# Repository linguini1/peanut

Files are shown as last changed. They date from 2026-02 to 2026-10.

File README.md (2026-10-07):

# Peanut 

A modern, tiny, and hackable altimeter for hobby rocketry.

[Peanut is certified as open-source hardware by the Open Source Hardware
Association (CA000081).][oshw-cert]

<p align="center">
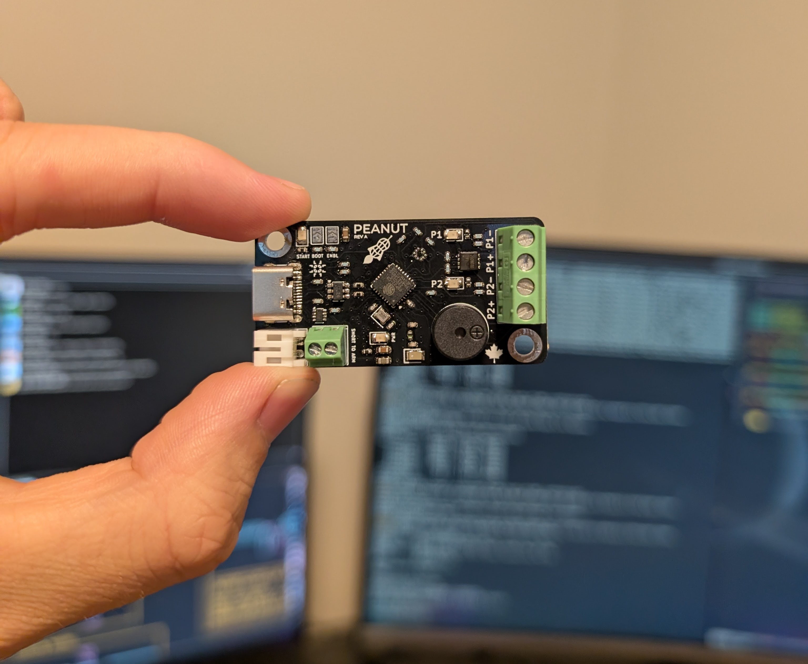
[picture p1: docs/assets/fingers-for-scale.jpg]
    
    <br/>
    Peanut Altimeter with my fingers for scale
</p>

<p align="center">
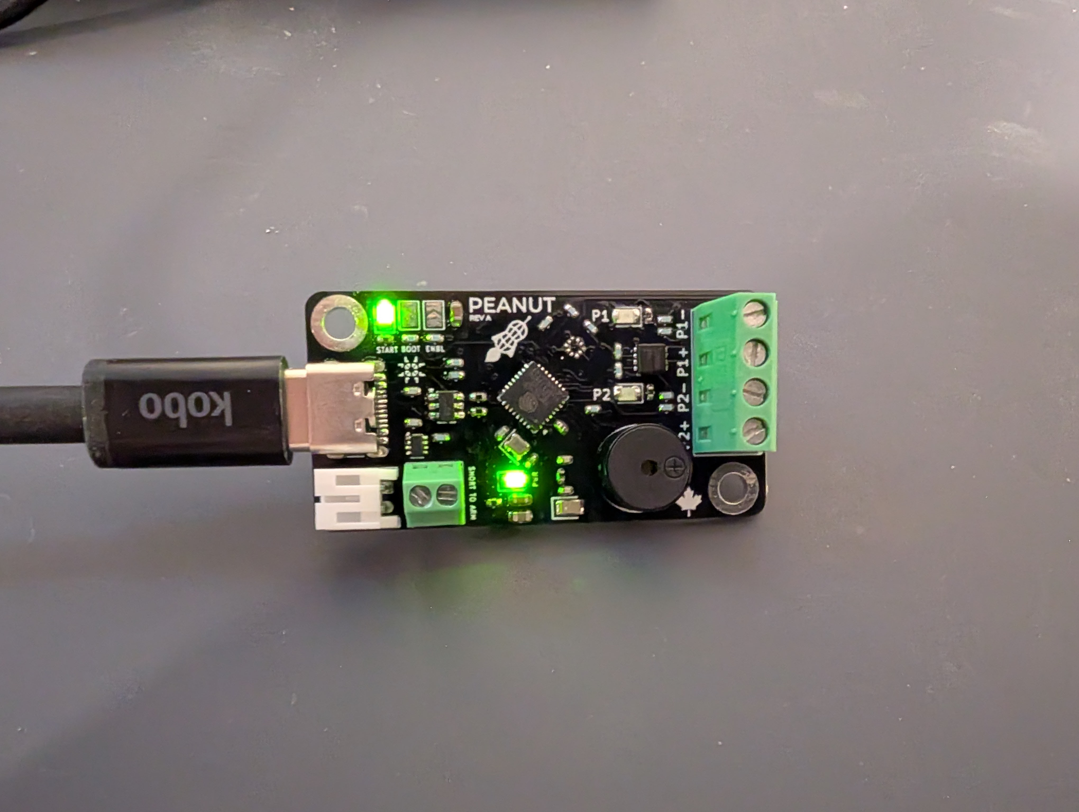
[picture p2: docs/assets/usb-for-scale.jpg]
    
    <br/>
    Peanut Altimeter powered up and operational
</p>

<p align="center">
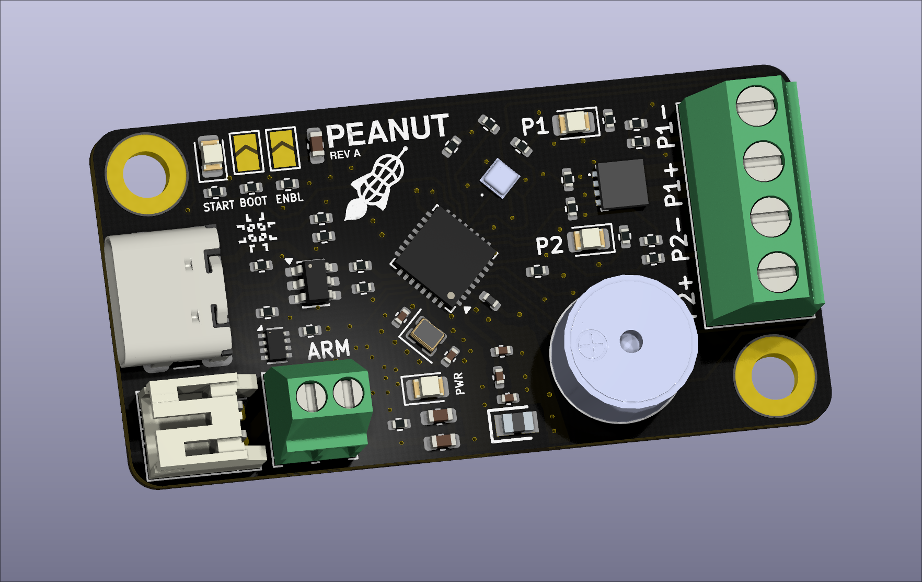
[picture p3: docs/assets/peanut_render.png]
    
    <br/>
    Peanut Altimeter KiCAD render
</p>

**Features include:**

* Fits in a min-diameter 29mm rocket
* High accuracy barometric pressure sensor (up to ~9km)
* Dual deploy capable (two pyro channels, >1A each)
* Continuity LED indicators for each pyro channel
* Battery reverse polarity protection
* On-board 2MB storage (4MB, 2MB for program, 2MB for logs)
  * Altitude measurements
  * Flight events (ascent, apogee, landing, etc.)
  * Deployment events
* Mach dip filtering (works on flights that break Mach)
* Buzzer arming indicator
* Bluetooth connection
  * Deployment ground testing with flight simulations over BLE
  * Wireless configuration
  * Battery life monitoring
  * Arming verification
  * Continuity & other telemetry over BLE
* WiFi capable

**Tech specs:**

* ESP32C3 MCU (4MB flash, 40KB RAM)
* BMP581 barometer
  * Configured with interrupt line for measurements
  * I2C operated
* Piezo buzzer with GPIO control
* ACAG0201-2450-T 2.4GHz PCB antenna

[Take a look at Peanut's layout and electrical schematics here.][kicad-view]

Peanut is also the subject of one of my [2026 Apache Community over
Code conference presentations][coc-alt-pres]. I discuss the process of designing
an altimeter with NuttX in mind, as well as what considerations go into robust
firmware design.

**Thank you to [PCBWay][pcbway] for sponsoring the manufacture of this project's
PCBs!**

## Firmware

The firmware for this board is made using the [Apache NuttX RTOS][nuttx-site],
an open-source embedded RTOS with an incredible community and an excellent
feature set.

Firmware is spread across a few repositories. If you are compiling yourself,
you'll need:
- [The NuttX kernel source][nuttx]
- [The NuttX application library][nuttx-apps]
- [The Peanut board support package (BSP)][peanut-bsp]
- [My application-level altimeter software,
  `rocket-altimeter`][rocket-altimeter]

Instructions for how to configure, compile and flash firmware can be found in
the [Peanut BSP][peanut-bsp] and [`rocket-altimeter`][rocket-altimeter]
repositories. Pre-built firmware binaries are made available with each release
under the [Peanut BSP][peanut-bsp] repository.

## Hackability

All hardware designs & firmware for Peanut are open-sourced and available under
permissive licensing.

The device itself is programmable over the USB-C interface using Espressif's
`esptool`, so users can tweak the firmware or write their own and easily
re-program the device. Want the buzzer to play custom audio? Want to change the
meaning of the "START" LED? Want to add more features to the Bluetooth
interface, or make the altimeter operate over WiFi instead? You can program
whatever you want into it!

## Physical Integration

If you'd like to fly Peanut, take a look at [the 3D models](./models) so you can
design your av-bay in CAD. This directory also contains the key dimensions of
Peanut for size and mounting holes.

**NOTE:** A user manual for Peanut is coming soon! For now, be aware that Peanut
is only rated for 4V2 LiPo/Li-ion batteries (3V7 nominal). You should only use
batteries _without overcurrent protection_ if you are flying Peanut for
deployment purposes. Otherwise, pyro channels may not be able to draw sufficient
current when fired.

## Make Your Own

If you want to make your own Peanut Altimeter, the component cost for the board
is roughly $35 CAD. You can get PCB blanks from a manufacturer of your choice
(i.e. PCBWay). You should only need to verify the trace widths of the
Bluetooth RF trace depending on the differences between your manufacturer's
PCB stackup and mine.

**NOTE:** This board was not designed with hand-soldering in mind (aside from
the backside). My manufacture process is to use solder paste, a stencil and a
hot plate to do the top-side components. There are 0402 components which are
manageable with steady hands and tweezers.

## On PCBWay

My experience using PCBWay could not have been easier. They provide a plugin for
KiCAD that directly exports your manufacturing files for order to their web
quote interface. I only hand to click the button and choose some parameters for
my board to get everything ordered.

My designs arrived on time, well package and the stencil was really high quality
with a large aluminum frame. I had no issues with the fine details (in copper
and on silkscreen) with such a small board, PCBWay nailed it.

[nuttx]: https://github.com/apache/nuttx
[nuttx-apps]: https://github.com/apache/nuttx-apps
[nuttx-site]: https://nuttx.apache.org/
[rocket-altimeter]: https://github.com/linguini1/rocket-altimeter
[peanut-bsp]: https://github.com/linguini1/peanut-bsp
[pcbway]: https://www.pcbway.com/
[kicad-view]: https://kicanvas.org/?github=https%3A%2F%2Fgithub.com%2Flinguini1%2Fpeanut%2Ftree%2Fmain%2Fpeanut
[coc-alt-pres]: https://web.cvent.com/event/ac71ce47-2b5f-424c-abfe-5b48255315fb/summary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
[oshw-cert]: https://certification.oshwa.org/ca000081.html

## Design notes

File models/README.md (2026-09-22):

# Peanut Models

This directory contains a collection of 3D models of Peanut if you want to
include it in your rocket.

* `peanut-board.step`: Just the board and mounting holes, no components
* `peanut-board.stl`: Same as above, but as an STL
* `peanut.step`: Board, mounting holes and components
* `peanut.stl`: Same as above, but as an STL

**NOTE:** It is recommended to check clearances using the models with components
populated. The buzzer is non-negligibly tall, and there are also components on
the underside of Peanut that prevent it from being seated completely flush to a
flat surface. Certainly don't mount it flush against anything conductive.

## Peanut Dimensions

* The board for Peanut is 24.5mm x 48.25mm with rounded corners
* Mounting holes are placed at opposite diagonals
* Mounting holes are centred on a rectangle of dimensions 18mm x 41mm
* Mounting holes are designed for M3 socket cap screws

Note that although the mounting holes are plated, they are electrically isolated
(not grounded, nor powered).

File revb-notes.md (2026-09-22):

# Revision B Notes

Notes for improvements that could be made to Revision B.

- BMP581 so far is incredibly unreliable in manufacturing. It would be good to
  pick another barometer that:
  - Is easier to solder (not LGA)
  - Has an interrupt line
  - Has an I2C interface
  - Possibly has a higher maximum altitude
  - Comparable sampling rate and reasonable precision

- Battery voltage divider might be better suited to have higher sensitivity in
  the range of 3V2 to 4V2 instead of from 0V to 4V2.
  - Connected batteries shouldn't drop below a certain minimum voltage (above
    0V)
  - The device will brown-out on the LDO before 3V3/3V2 anyways

- I2C pull-ups should be 2k2, 10k is a little high and it's not saving much cost

- Is a PWM buzzer a good idea? For playing jingles?

- Ensure manufacturer removes serial number from silkscreen

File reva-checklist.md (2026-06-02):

# Review Checklist

A list of things that need to be checked for the design to sufficiently verified
for order.

## Basics

- [x] Schematic ERC passes
- [x] PCB DRC passes
- [x] PCB stack-up matches what is available on JLC/PCBWay
- [x] PCB design rules match the capabilities of JLC/PCBWay

## Components

- [x] Each component has a BOM MPN that is in stock on Mouser/Digikey
- [x] Pin assignment to component footprint is correct (check _all_
      non-passives)
  - [x] Clock
  - [x] GPIO NMOS
  - [x] Pyro NMOS
  - [x] PMOS
  - [x] MCU
  - [x] Barometer
  - [x] USB
  - [x] Regulator
  - [x] Power MUX
- [x] Connections to FETs are correct
- [x] Battery leads have right polarity

NOTE: made battery leads follow the shitty standard set out by other rocket
electronics where pin 1 is V+ and pin 2 is GND.

## Component Ratings

- [x] Component values are correct for their use (correct resistance,
      capacitance, etc.)
- [x] Components passing high power have sufficient wattage
- [x] LED circuits are properly connected for forward voltage + resistance
- [x] FETs have correct activation voltage
- [x] FETs can pass sufficient current
- [x] Max current draw can be supplied by the regulator
- [x] RF matching circuitry has correct values

## Correctness

- [x] All LEDs have resistors
- [x] All switching NMOS FETs have gate pull-downs
- [x] Voltage dividers are correct for all possible input/output ranges
- [x] Load capacitance for clock is correct
- [x] Boot/enable circuitry is correct for MCU
- [x] Pin assignments for MCU are correct
- [x] Pin assignments for barometer are correct

## Routing

- [x] High current traces can supply sufficient current
- [x] Via stitching around clock
- [x] Via stitching around RF trace
- [x] USB routed as 90ohm differential pair
- [x] RF routed as 50ohm impedance matched
- [ ] RF trace below critical length (not really but best I can do)
- [ ] RF routing matches application note suggestion (antenna/ESP32) (not really
      but best I can do)
- [x] All fill zones poured
- [x] Minimal 0402 sized components on back, only if hand-solderable

## Silkscreen

- [x] Logo is visible on top side
- [x] Revision is visible on top side
- [x] Pyro channels are clearly labelled
- [x] All LEDs are clearly labelled
- [x] Arming terminal is clearly labelled
- [x] Boot jumpers are clearly labelled
- [x] Components on back-side are sufficiently short for mounting
- [x] Mounting holes have a hole pattern with distances in whole millimeters

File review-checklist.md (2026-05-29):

# Review Checklist

A list of things that need to be checked for the design to sufficiently verified
for order.

## Basics

- [ ] Schematic ERC passes
- [ ] PCB DRC passes
- [ ] PCB stack-up matches what is available on JLC/PCBWay
- [ ] PCB design rules match the capabilities of JLC/PCBWay

## Components

- [ ] Each component has a BOM MPN that is in stock on Mouser/Digikey
- [ ] Pin assignment to component footprint is correct (check _all_
      non-passives)
  - [ ] Clock
  - [ ] GPIO NMOS
  - [ ] Pyro NMOS
  - [ ] PMOS
  - [ ] MCU
  - [ ] Barometer
  - [ ] USB
  - [ ] Regulator
  - [ ] Power MUX
- [ ] Connections to FETs are correct
- [ ] Battery leads have right polarity

## Component Ratings

- [ ] Component values are correct for their use (correct resistance,
      capacitance, etc.)
- [ ] Components passing high power have sufficient wattage
- [ ] LED circuits are properly connected for forward voltage + resistance
- [ ] FETs have correct activation voltage
- [ ] FETs can pass sufficient current
- [ ] Max current draw can be supplied by the regulator
- [ ] RF matching circuitry has correct values

## Correctness

- [ ] All LEDs have resistors
- [ ] All switching NMOS FETs have gate pull-downs
- [ ] Voltage dividers are correct for all possible input/output ranges
- [ ] Load capacitance for clock is correct
- [ ] Boot/enable circuitry is correct for MCU
- [ ] Pin assignments for MCU are correct
- [ ] Pin assignments for barometer are correct

## Routing

- [ ] High current traces can supply sufficient current
- [ ] Via stitching around clock
- [ ] Via stitching around RF trace
- [ ] USB routed as 90ohm differential pair
- [ ] RF routed as 50ohm impedance matched
- [ ] RF trace below critical length
- [ ] RF routing matches application note suggestion (antenna/ESP32)
- [ ] All fill zones poured
- [ ] Minimal 0402 sized components on back, only if hand-solderable

## Silkscreen

- [ ] Logo is visible on top side
- [ ] Revision is visible on top side
- [ ] Pyro channels are clearly labelled
- [ ] All LEDs are clearly labelled
- [ ] Arming terminal is clearly labelled
- [ ] Boot jumpers are clearly labelled
- [ ] Components on back-side are sufficiently short for mounting
- [ ] Mounting holes have a hole pattern with distances in whole millimeters

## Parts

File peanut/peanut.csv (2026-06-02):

Reference | Qty | MPN | Value | DNP | Footprint | Datasheet
AE1 | 1 | ACAG0201-2450-T | BLE Antenna |  | ACAG0201-2450-T:ANTC2012X70N | https://www.mouser.ca/datasheet/3/184/1/ACAG0201_2450_T.pdf
BZ1 | 1 | CMI-0955-03TH | Buzzer |  | CMI-0955-03TH:CMI095503TH | https://www.mouser.ca/datasheet/3/6118/1/cmi_0955_03th.pdf
C1,C3,C5,C9,C11 | 5 | KGM15AR70J104KT | 100n |  | Capacitor_SMD:C_0603_1608Metric | https://ele.kyocera.com/assets/products/capacitor/KGM_Series_e.pdf
C2,C6,C7,C10,C18,C19,C20 | 7 | 06036C105MAT2A | 1u |  | Capacitor_SMD:C_0603_1608Metric
C4,C17 | 2 | C1608X5R0J106K080AB | 10u |  | Capacitor_SMD:C_0603_1608Metric
C8 | 1 | MBASU105SB5103KFNA18 | 10n |  | Capacitor_SMD:C_0402_1005Metric | https://ds.yuden.co.jp/TYCOMPAS/or/download?pn=MBARQ167SCG0R4ATRA01&fileType=CS
C12,C14 | 2 | GRM1555C1E8R0DA01D | 8p |  | Capacitor_SMD:C_0402_1005Metric | https://www.mouser.ca/datasheet/3/76/1/GRM1555C1E8R0DA01-01A.pdf
C13,C15 | 2 | RF15N1R6B500CT | 1p6 |  | Capacitor_SMD:C_0402_1005Metric | https://www.mouser.ca/datasheet/3/317/1/Microwave_Caps.pdf
C16 | 1 | MLASJ168BB5226MTNA01 | 22u |  | Capacitor_SMD:C_0603_1608Metric
D1,D5 | 2 | HSMG-C170 | GREEN |  | LED_SMD:LED_0805_2012Metric
D2 | 1 | SS25FA |  |  | Diode_SMD:D_SOD-123F | https://www.onsemi.com/pub/Collateral/SS29FA-D.PDF
D3,D4 | 2 | 599-1140-147F | YELLOW |  | LED_SMD:LED_0805_2012Metric
D6 | 1 | PDZ4.3BZ | 4V5 |  | Diode_SMD:D_SOD-323_HandSoldering
J1 | 1 | USB4215-03-A | USB-C |  | Connector_USB:USB_C_Receptacle_GCT_USB4105-xx-A_16P_TopMnt_Horizontal | https://www.usb.org/sites/default/files/documents/usb_type-c.zip
J2 | 1 | 1727036 | PYRO_OUT |  | TerminalBlock_Phoenix:TerminalBlock_Phoenix_MKDS-1-4-3.81_1x04_P3.81mm_Horizontal | https://www.mouser.ca/datasheet/3/507/9/phoenix_contact_1727036_en.pdf
J3 | 1 | S2B-PH-K-S(LF)(SN)(PP) | Battery JST |  | Connector_JST:JST_PH_S2B-PH-K_1x02_P2.00mm_Horizontal | https://www.jst-mfg.com/product/pdf/eng/ePH.pdf
J4 | 1 | 1725656 | Arming |  | TerminalBlock_Phoenix:TerminalBlock_Phoenix_MPT-0,5-2-2.54_1x02_P2.54mm_Horizontal | https://www.mouser.ca/datasheet/3/507/9/phoenix_contact_1725656_en.pdf
JP1,JP2 | 2 |  | RESET |  | Jumper:SolderJumper-2_P1.3mm_Open_TrianglePad1.0x1.5mm
L1 | 1 | 36550402S2N0T | 2n |  | Inductor_SMD:L_0402_1005Metric | https://www.te.com/commerce/DocumentDelivery/DDEController?Action=showdoc
L2 | 1 | LQG15WZ2N6B02D | 2n6 |  | Capacitor_SMD:C_0402_1005Metric | https://www.mouser.ca/datasheet/3/76/2/JELF243B_9117.pdf
Q1,Q2,Q3 | 3 | BSS123NH6327XTSA1 | NMOS |  | Package_TO_SOT_SMD:SOT-23-3 | https://www.mouser.ca/datasheet/3/70/1/Infineon_BSS123N_DataSheet_v02_03_en.pdf
Q4 | 1 | TSM200N03DPQ33 RGG | NMOS |  | TSM200N03DPQ33_RGG:TSM200N03DPQ33RGG
Q5 | 1 | SI2329DS-T1-GE3 | PMOS |  | Package_TO_SOT_SMD:SOT-23 | https://ngspice.sourceforge.io/docs/ngspice-html-manual/manual.xhtml#cha_MOSFETs
R1,R2,R8,R9,R10,R11,R12,R14,R15,R17,R18,R19,R20,R21,R24 | 15 | MCS04020C1002FE000 | 10k |  | Resistor_SMD:R_0402_1005Metric
R3,R4 | 2 | MCS04020C5101FE000 | 5k1 |  | Resistor_SMD:R_0402_1005Metric
R5,R13,R16,R22 | 4 | 560112110231 | 330R |  | Resistor_SMD:R_0402_1005Metric
R6,R7 | 2 | ERA-2AKD270X | 27R |  | Resistor_SMD:R_0402_1005Metric
R23 | 1 | ERA-3AED104V | 100k |  | Resistor_SMD:R_0603_1608Metric
U1 | 1 | BMP581 | BMP581 |  | BMP581:BMP581 | https://www.bosch-sensortec.com/media/boschsensortec/downloads/datasheets/bst-bmp581-ds004.pdf
U2 | 1 | USBLC6-2SC6 |  |  | Package_TO_SOT_SMD:SOT-23-6 | https://www.st.com/resource/en/datasheet/usblc6-2.pdf
U3 | 1 | ESP32-C3FH4 | ESP32-C3FH4 |  | Package_DFN_QFN:QFN-32-1EP_5x5mm_P0.5mm_EP3.7x3.7mm | https://www.espressif.com/sites/default/files/documentation/esp32-c3_datasheet_en.pdf
U4 | 1 | MCP1826S-3302E/DB | MCP1826S |  | Package_TO_SOT_SMD:SOT-223-3_TabPin2 | http://ww1.microchip.com/downloads/en/DeviceDoc/22057B.pdf
U5 | 1 | TPS2116DRLR | TPS2116DRL |  | Package_TO_SOT_SMD:SOT-583-8 | https://www.ti.com/lit/ds/symlink/tps2116.pdf
Y1 | 1 | 830108213209 | 40MHz +/-10ppm |  | Crystal:Crystal_SMD_2016-4Pin_2.0x1.6mm | https://www.we-online.com/components/products/datasheet/830108213209.pdf

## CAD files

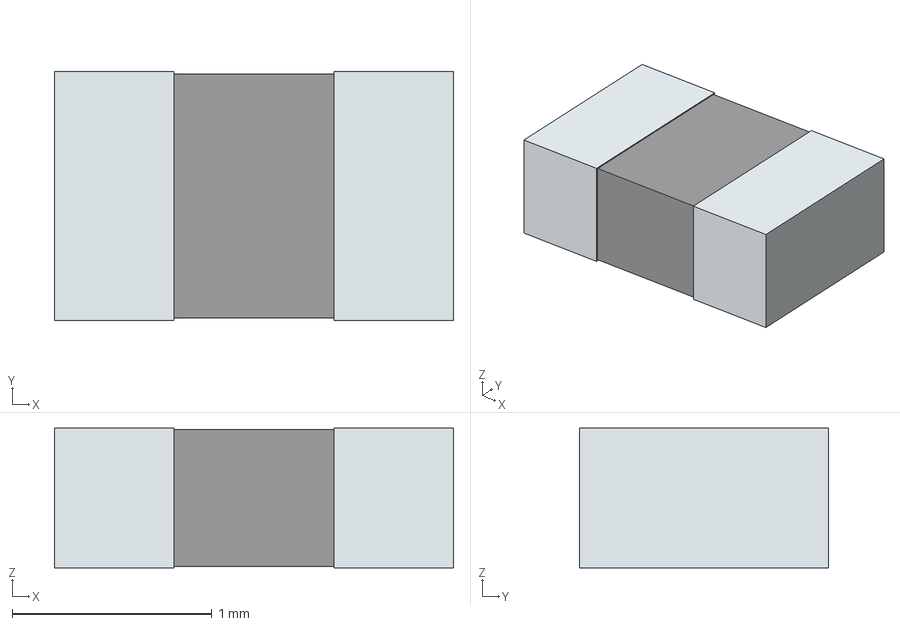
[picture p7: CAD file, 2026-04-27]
LIB_ACAG0201-2450-T/3D/ACAG0201-2450-T.stp
2.00 x 1.25 x 0.7 mm
term1
term2

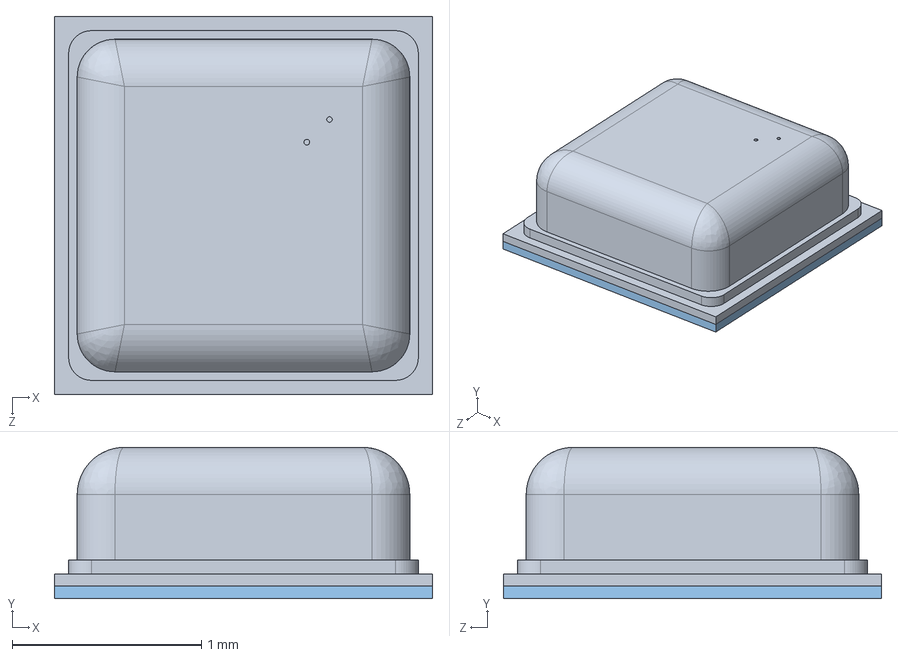
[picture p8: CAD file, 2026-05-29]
LIB_BMP581/3D/BMP581.stp
2.00 x 0.801 x 2.00 mm

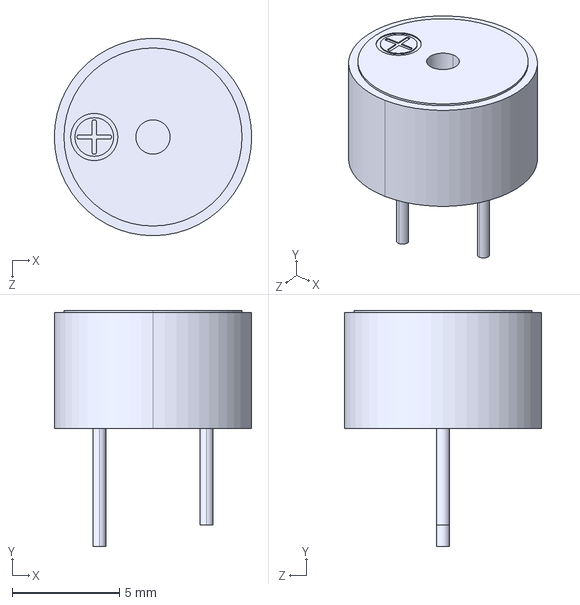
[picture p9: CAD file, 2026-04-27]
LIB_CMI-0955-03TH/3D/CMI-0955-03TH.stp
9.20 x 11.0 x 9.20 mm

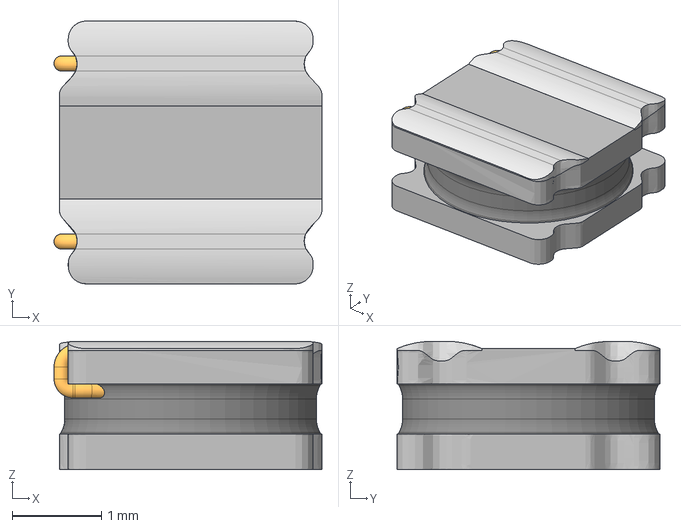
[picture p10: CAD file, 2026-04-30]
LIB_SRN3015BTA-2R2M/3D/SRN3015BTA-2R2M.stp
3.01 x 2.96 x 1.44 mm

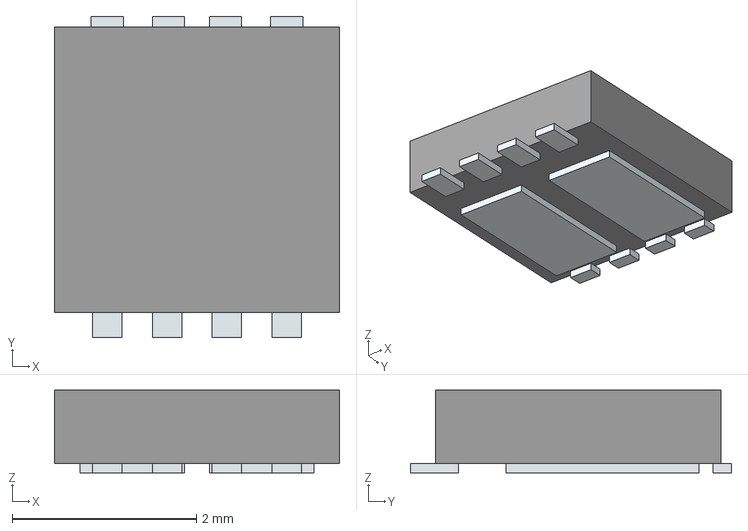
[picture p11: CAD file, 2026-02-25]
LIB_TSM200N03DPQ33_RGG/3D/TSM200N03DPQ33_RGG.stp
3.10 x 3.49 x 0.9 mm
Pins

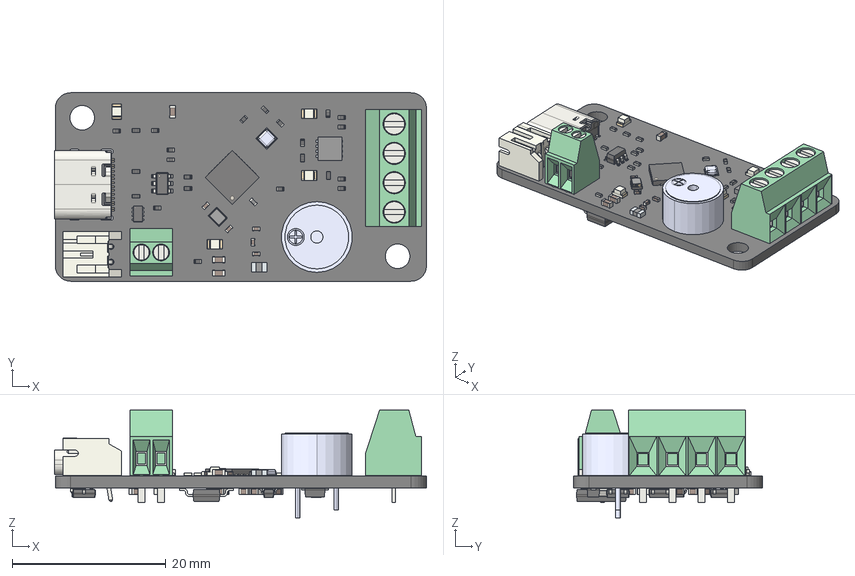
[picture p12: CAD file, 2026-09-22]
models/peanut.step
48.3 x 24.5 x 14.0 mm
R_0402_1005Metric x 23
C_0402_1005Metric x 6
C_0603_1608Metric x 15
SOT-583-8
TerminalBlock_Phoenix_MKDS-1-4-3.81_1x04_P3.81mm_Horizontal
LED_0805_2012Metric x 4
term1
term2
L_0402_1005Metric
TerminalBlock_Phoenix_MPT-0,5-2-2.54_1x02_P2.54mm_Horizontal
Same_Sky_CMI-0955-03TH
BMP581
JST_S2B_PH_K
SOT-23-6
Crystal_SMD_2016-4Pin_2.0x1.6mm
Pins
USB_C_Receptacle_16P_TopMnt_Horizontal_GCT_USB4105-xx-A
QFN-32-1EP_5x5mm_P0.5mm_EP3.7x3.7mm
D_SOD_123F
SOT-23
SOT-223
D_SOD-323
SOT-23-3 x 3
R_0603_1608Metric
peanut-unsaved-export-IKAy2I_PCB

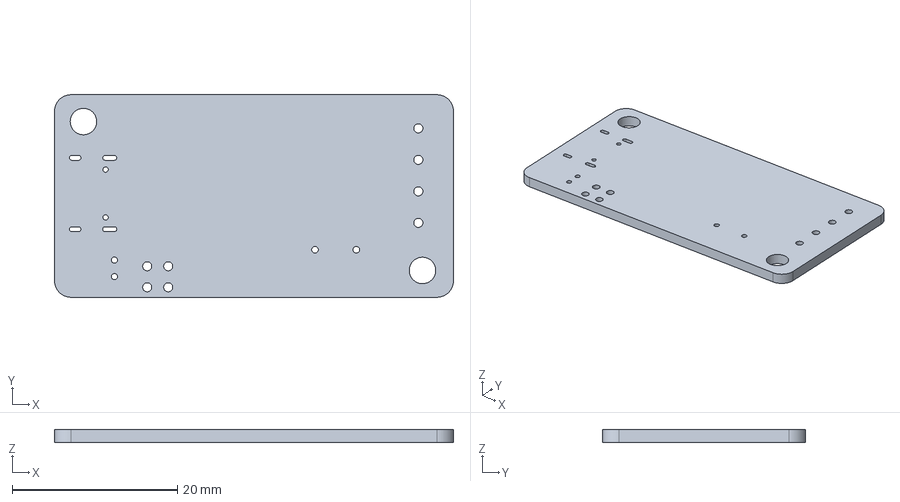
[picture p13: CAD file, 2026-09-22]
models/peanut-board.step
48.2 x 24.5 x 1.52 mm

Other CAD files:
models/peanut-board.stl
models/peanut.stl

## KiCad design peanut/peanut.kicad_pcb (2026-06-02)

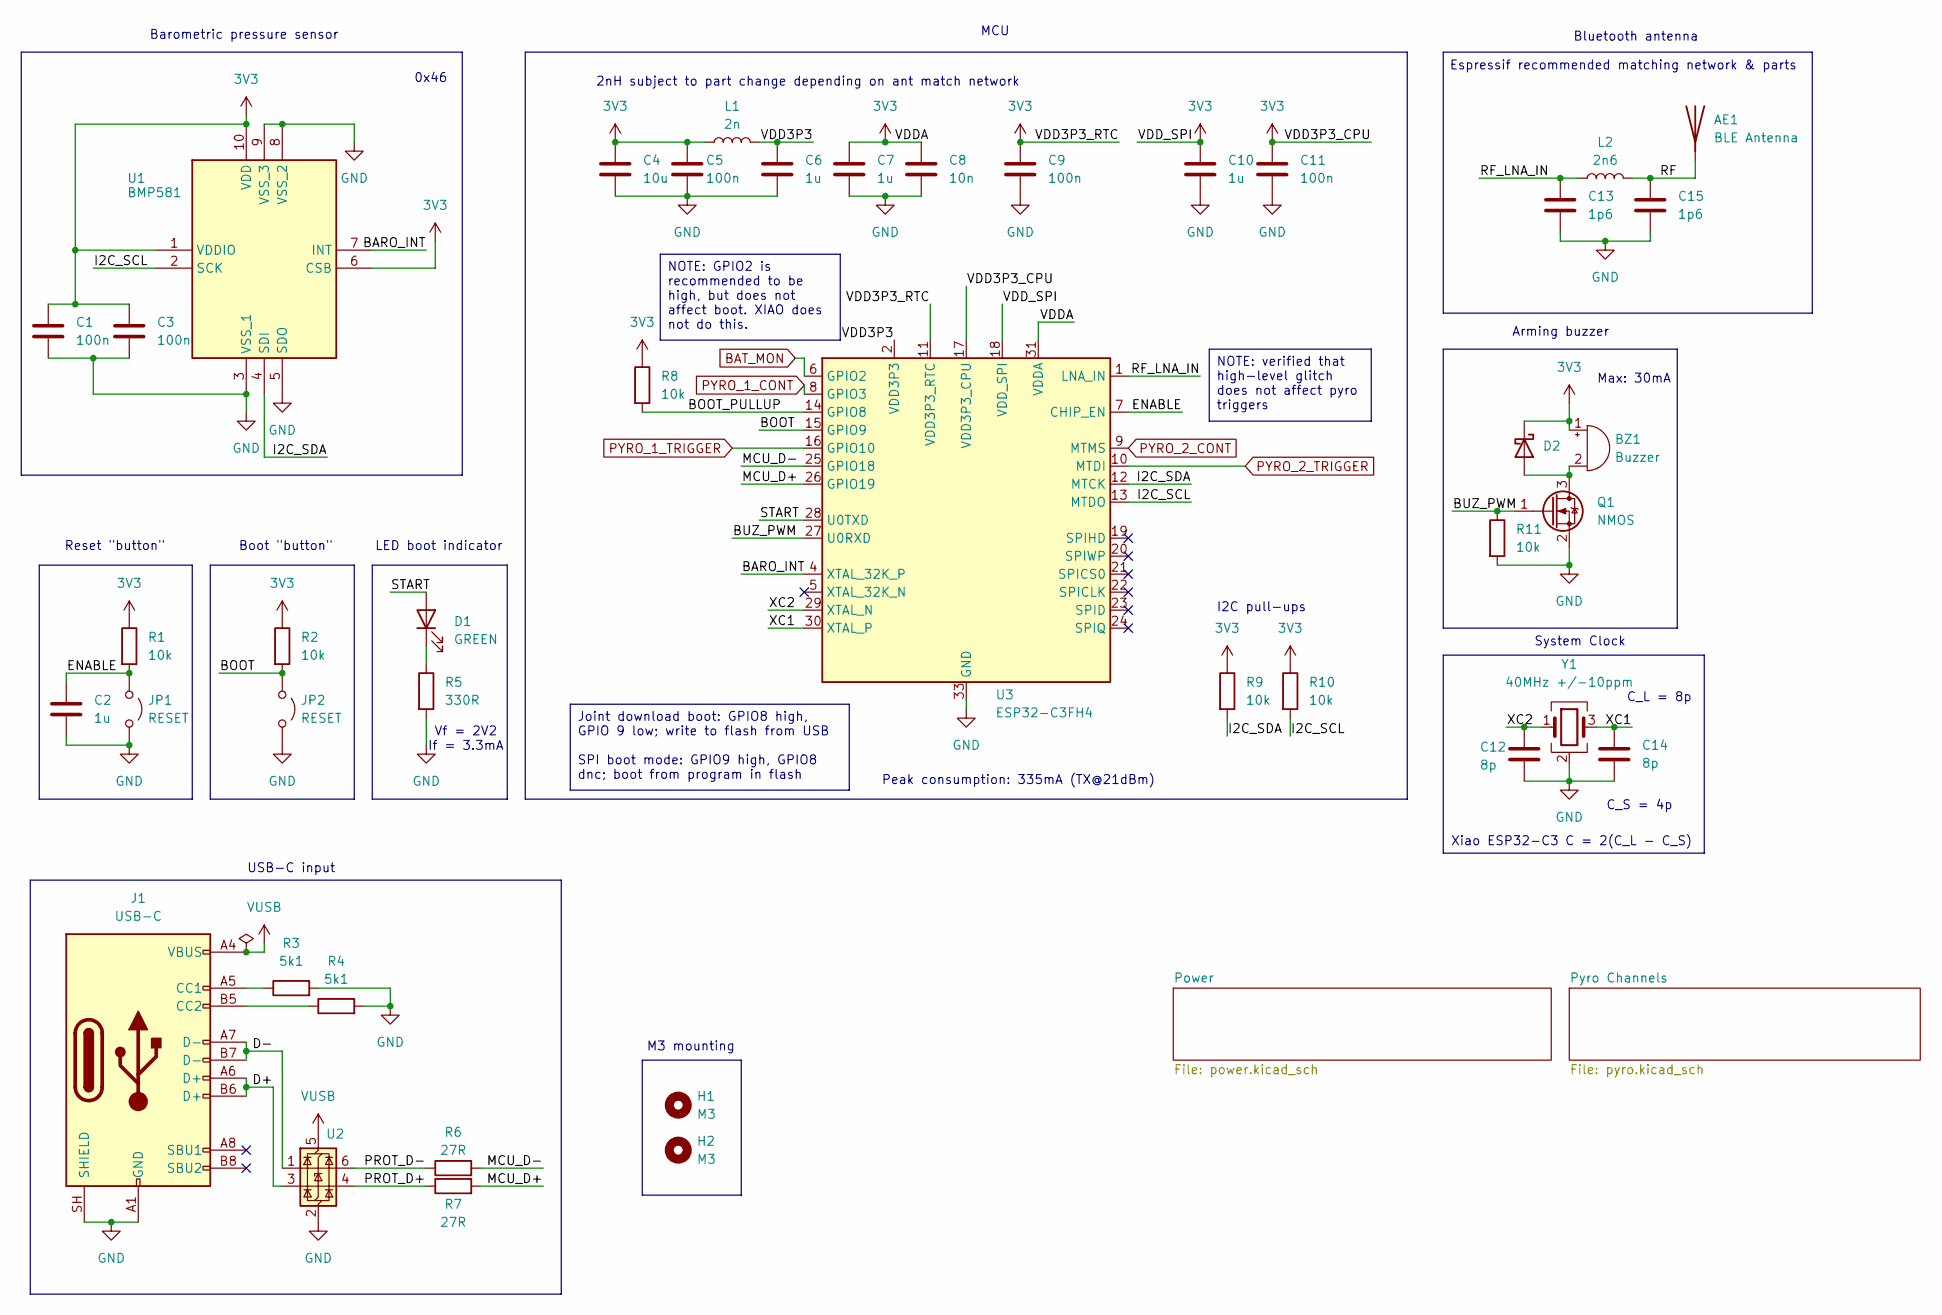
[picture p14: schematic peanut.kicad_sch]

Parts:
AE1: BLE Antenna; ANTC2012X70N; MPN ACAG0201-2450-T
BZ1: Buzzer; CMI095503TH; MPN CMI-0955-03TH
C1, C3, C5, C9, C11: 100n; C_0603_1608Metric; MPN KGM15AR70J104KT
C2, C6, C7, C10: 1u; C_0603_1608Metric; MPN 06036C105MAT2A
C4: 10u; C_0603_1608Metric; MPN C1608X5R0J106K080AB
C8: 10n; C_0402_1005Metric; MPN MBASU105SB5103KFNA18
C12, C14: 8p; C_0402_1005Metric; MPN GRM1555C1E8R0DA01D
C13, C15: 1p6; C_0402_1005Metric; MPN RF15N1R6B500CT
D1: GREEN; LED_0805_2012Metric; MPN HSMG-C170
D2: D_SOD-123F; MPN SS25FA
H1, H2: M3; MountingHole_3.2mm_M3_DIN965_Pad_TopOnly
J1: USB-C; USB_C_Receptacle_GCT_USB4105-xx-A_16P_TopMnt_Horizontal; MPN USB4215-03-A
JP1, JP2: RESET; SolderJumper-2_P1.3mm_Open_TrianglePad1.0x1.5mm
L1: 2n; L_0402_1005Metric; MPN 36550402S2N0T
L2: 2n6; C_0402_1005Metric; MPN LQG15WZ2N6B02D
Q1: NMOS; SOT-23-3; MPN BSS123NH6327XTSA1
R1, R2, R8, R9, R10, R11: 10k; R_0402_1005Metric; MPN MCS04020C1002FE000
R3, R4: 5k1; R_0402_1005Metric; MPN MCS04020C5101FE000
R5: 330R; R_0402_1005Metric; MPN 560112110231
R6, R7: 27R; R_0402_1005Metric; MPN ERA-2AKD270X
U1: BMP581; Mouser Part Number 262-BMP581
U2: SOT-23-6; MPN USBLC6-2SC6
U3: ESP32-C3FH4; QFN-32-1EP_5x5mm_P0.5mm_EP3.7x3.7mm; MPN ESP32-C3FH4
Y1: 40MHz +/-10ppm; Crystal_SMD_2016-4Pin_2.0x1.6mm; MPN 830108213209

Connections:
3V3: BZ1.1 (+), C1.1, C3.1, C4.1, C5.1, C7.1, C8.1, C9.1, C10.1, C11.1, D2.1 (K), L1.1, R1.1, R2.1, R8.1, R9.1, R10.1, U1.1 (VDDIO), U1.6 (CSB), U1.10 (VDD), U3.11 (VDD3P3_RTC), U3.17 (VDD3P3_CPU), U3.18 (VDD_SPI), U3.31 (VDDA), U3.32 (VDDA); also elsewhere on the board
/BARO_INT: U1.7 (INT), U3.4 (XTAL_32K_P)
/BOOT: JP2.1 (A), R2.2, U3.15 (GPIO9)
/BOOT_PULLUP: R8.2, U3.14 (GPIO8)
/BUZ_PWM: Q1.1 (G), R11.1, U3.27 (U0RXD)
/D+: J1.A6 (D+), J1.B6 (D+), U2.3 (I/O2)
/D-: J1.A7 (D-), J1.B7 (D-), U2.1 (I/O1)
/ENABLE: C2.1, JP1.1 (A), R1.2, U3.7 (CHIP_EN)
/I2C_SCL: R10.2, U1.2 (SCK), U3.13 (MTDO)
/I2C_SDA: R9.2, U1.4 (SDI), U3.12 (MTCK)
/MCU_D+: R7.2, U3.26 (GPIO19)
/MCU_D-: R6.2, U3.25 (GPIO18)
/PROT_D+: R7.1, U2.4 (I/O2)
/PROT_D-: R6.1, U2.6 (I/O1)
/RF: AE1.1 (A_1), C15.1, L2.2
/RF_LNA_IN: C13.1, L2.1, U3.1 (LNA_IN)
/START: D1.2 (A), U3.28 (U0TXD)
/VDD3P3: C6.1, L1.2, U3.2 (VDD3P3), U3.3 (VDD3P3)
/XC1: C14.1, U3.30 (XTAL_P), Y1.3
/XC2: C12.1, U3.29 (XTAL_N), Y1.1
BAT_MON: U3.6 (GPIO2); also elsewhere on the board
GND: C1.2, C2.2, C3.2, C4.2, C5.2, C6.2, C7.2, C8.2, C9.2, C10.2, C11.2, C12.2, C13.2, C14.2, C15.2, J1.A1 (GND), J1.A12 (GND), J1.B1 (GND), J1.B12 (GND), J1.SH (SHIELD), JP1.2 (B), JP2.2 (B), Q1.2 (S), R3.2, R4.2, R5.2, R11.2, U1.3 (VSS_1), U1.5 (SDO), U1.8 (VSS_2), U1.9 (VSS_3), U2.2 (GND), U3.33 (GND), Y1.2 (G), Y1.4 (G); also elsewhere on the board
unnamed: BZ1.2 (-), D2.2 (A), Q1.3 (D)
unnamed: D1.1 (K), R5.1
unnamed: J1.A5 (CC1), R3.1
unnamed: J1.B5 (CC2), R4.1
PYRO_1_CONT: U3.8 (GPIO3); also elsewhere on the board
PYRO_1_TRIGGER: U3.16 (GPIO10); also elsewhere on the board
PYRO_2_CONT: U3.9 (MTMS); also elsewhere on the board
PYRO_2_TRIGGER: U3.10 (MTDI); also elsewhere on the board
VUSB: J1.A4 (VBUS), J1.A9 (VBUS), J1.B4 (VBUS), J1.B9 (VBUS), U2.5 (VBUS); also elsewhere on the board

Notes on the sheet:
USB-C input
M3 mounting
Bluetooth antenna
Reset "button"
Espressif recommended matching network & parts
Peak consumption: 335mA (TX@21dBm)
I2C pull-ups
System Clock
Max: 30mA
Xiao ESP32-C3
Arming buzzer
2nH subject to part change depending on ant match network
LED boot indicator
0x46
Boot "button"
C = 2(C_L - C_S)
C_S = 4p
Barometric pressure sensor
Vf = 2V2 If = 3.3mA
MCU
C_L = 8p
Joint download boot: GPIO8 high, GPIO 9 low; write to flash from USB SPI boot mode: GPIO9 high, GPIO8 dnc; boot from program in flash
NOTE: verified that high-level glitch does not affect pyro triggers
NOTE: GPIO2 is recommended to be high, but does not affect boot. XIAO does not do this.

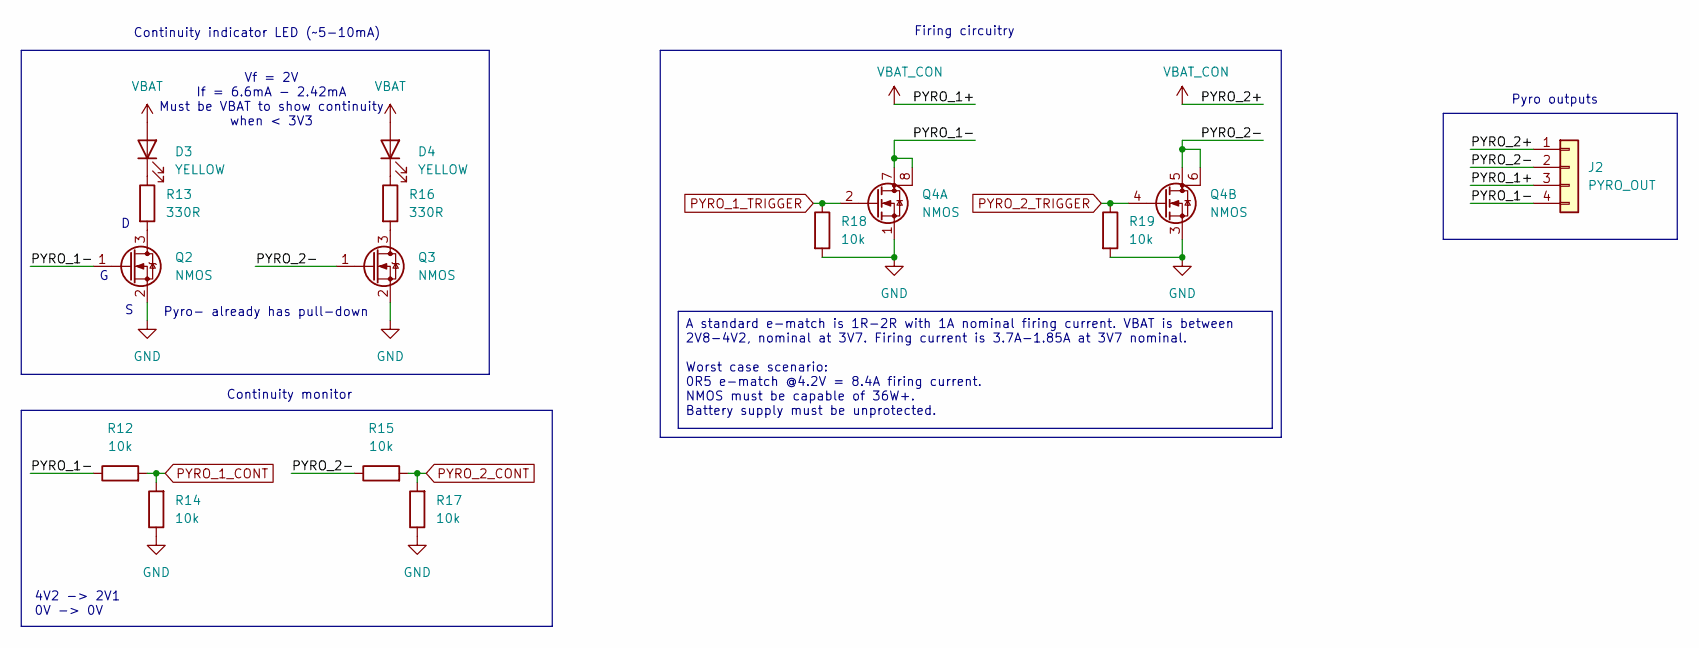
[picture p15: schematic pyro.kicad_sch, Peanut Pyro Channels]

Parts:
D3, D4: YELLOW; LED_0805_2012Metric; MPN 599-1140-147F
J2: PYRO_OUT; TerminalBlock_Phoenix_MKDS-1-4-3.81_1x04_P3.81mm_Horizontal; MPN 1727036
Q2, Q3: NMOS; SOT-23-3; MPN BSS123NH6327XTSA1
Q4: NMOS; TSM200N03DPQ33RGG; MPN TSM200N03DPQ33 RGG
R12, R14, R15, R17, R18, R19: 10k; R_0402_1005Metric; MPN MCS04020C1002FE000
R13, R16: 330R; R_0402_1005Metric; MPN 560112110231

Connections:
/Pyro Channels/PYRO_1-: J2.4, Q2.1 (G), Q4.7 (D), Q4.8 (D), Q4.10, R12.1
/Pyro Channels/PYRO_2-: J2.2, Q3.1 (G), Q4.5 (D), Q4.6 (D), Q4.9, R15.1
GND: Q2.2 (S), Q3.2 (S), Q4.1 (S), Q4.3 (S), R14.1, R17.1, R18.2, R19.2; also elsewhere on the board
unnamed: D3.1 (K), R13.1
unnamed: D4.1 (K), R16.1
unnamed: Q2.3 (D), R13.2
unnamed: Q3.3 (D), R16.2
PYRO_1_CONT: R12.2, R14.2; also elsewhere on the board
PYRO_1_TRIGGER: Q4.2 (G), R18.1; also elsewhere on the board
PYRO_2_CONT: R15.2, R17.2; also elsewhere on the board
PYRO_2_TRIGGER: Q4.4 (G), R19.1; also elsewhere on the board
VBAT: D3.2 (A), D4.2 (A); also elsewhere on the board
VBAT_CON: J2.1, J2.3; also elsewhere on the board

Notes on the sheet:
Firing circuitry
Pyro outputs
Vf = 2V If = 6.6mA - 2.42mA Must be VBAT to show continuity when < 3V3
4V2 -> 2V1 0V -> 0V
Continuity indicator LED (~5-10mA)
Pyro- already has pull-down
Continuity monitor
A standard e-match is 1R-2R with 1A nominal firing current. VBAT is between 2V8-4V2, nominal at 3V7. Firing current is 3.7A-1.85A at 3V7 nominal. Worst case scenario: 0R5 e-match @4.2V = 8.4A firing current. NMOS must be capable of 36W+. Battery supply must be unprotected.

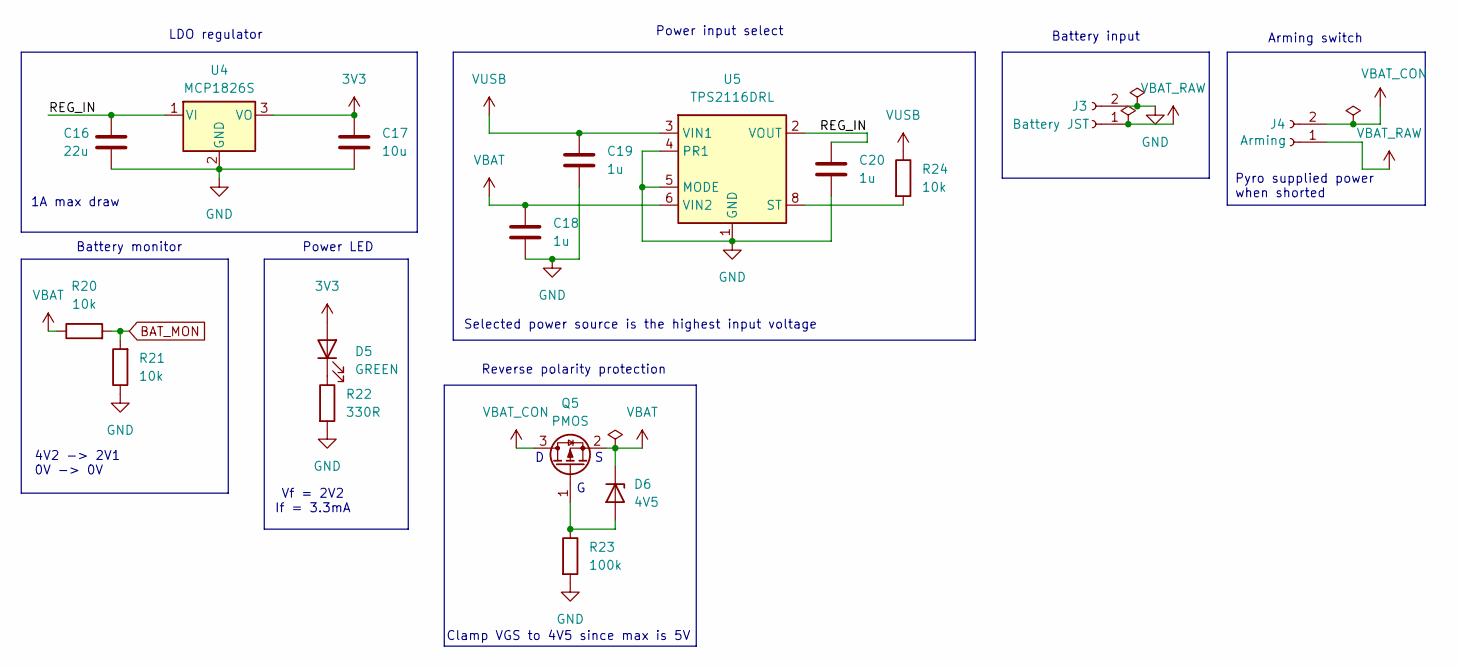
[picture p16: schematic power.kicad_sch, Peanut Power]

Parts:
C16: 22u; C_0603_1608Metric; MPN MLASJ168BB5226MTNA01
C17: 10u; C_0603_1608Metric; MPN C1608X5R0J106K080AB
C18, C19, C20: 1u; C_0603_1608Metric; MPN 06036C105MAT2A
D5: GREEN; LED_0805_2012Metric; MPN HSMG-C170
D6: 4V5; D_SOD-323_HandSoldering; MPN PDZ4.3BZ
J3: Battery JST; JST_PH_S2B-PH-K_1x02_P2.00mm_Horizontal; MPN S2B-PH-K-S(LF)(SN)(PP)
J4: Arming; TerminalBlock_Phoenix_MPT-0,5-2-2.54_1x02_P2.54mm_Horizontal; MPN 1725656
Q5: PMOS; SOT-23; MPN SI2329DS-T1-GE3
R20, R21, R24: 10k; R_0402_1005Metric; MPN MCS04020C1002FE000
R22: 330R; R_0402_1005Metric; MPN 560112110231
R23: 100k; R_0603_1608Metric; MPN ERA-3AED104V
U4: MCP1826S; SOT-223-3_TabPin2; MPN MCP1826S-3302E/DB
U5: TPS2116DRL; SOT-583-8; MPN TPS2116DRLR

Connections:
3V3: C17.1, D5.2 (A), U4.3 (VO); also elsewhere on the board
/Power/REG_IN: C16.1, C20.1, U4.1 (VI), U5.2 (VOUT), U5.7 (VOUT)
BAT_MON: R20.2, R21.2; also elsewhere on the board
GND: C16.2, C17.2, C18.2, C19.2, C20.2, J3.2, R21.1, R22.2, R23.2, U4.2 (GND), U5.1 (GND), U5.4 (PR1), U5.5 (MODE); also elsewhere on the board
unnamed: D5.1 (K), R22.1
unnamed: D6.2 (A), Q5.1 (G), R23.1
unnamed: R24.2, U5.8 (ST)
VBAT: C18.1, D6.1 (K), Q5.2 (S), R20.1, U5.6 (VIN2); also elsewhere on the board
VBAT_CON: J4.2, Q5.3 (D); also elsewhere on the board
VBAT_RAW: J3.1, J4.1
VUSB: C19.1, R24.1, U5.3 (VIN1); also elsewhere on the board

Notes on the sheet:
4V2 -> 2V1 0V -> 0V
LDO regulator
Vf = 2V2 If = 3.3mA
Clamp VGS to 4V5 since max is 5V
Reverse polarity protection
1A max draw
Battery monitor
Power input select
Arming switch
Battery input
Power LED
Selected power source is the highest input voltage
Pyro supplied power when shorted

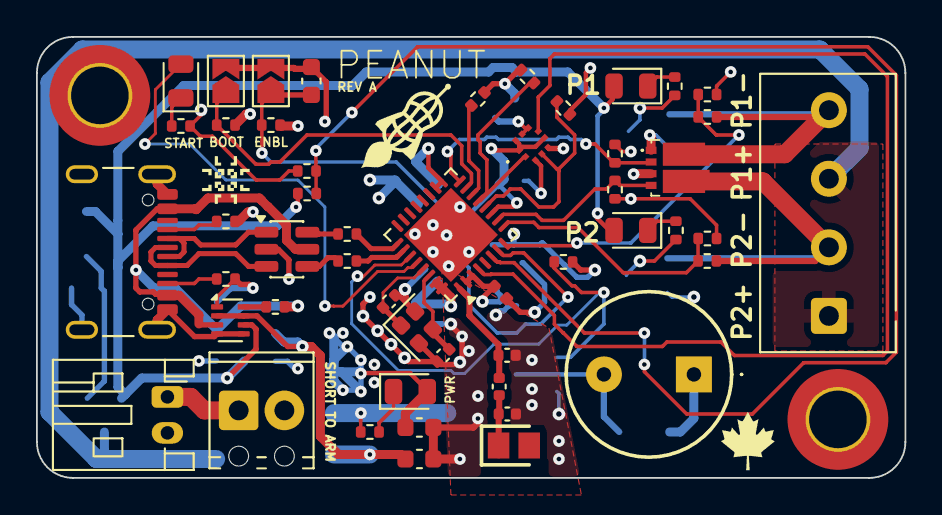
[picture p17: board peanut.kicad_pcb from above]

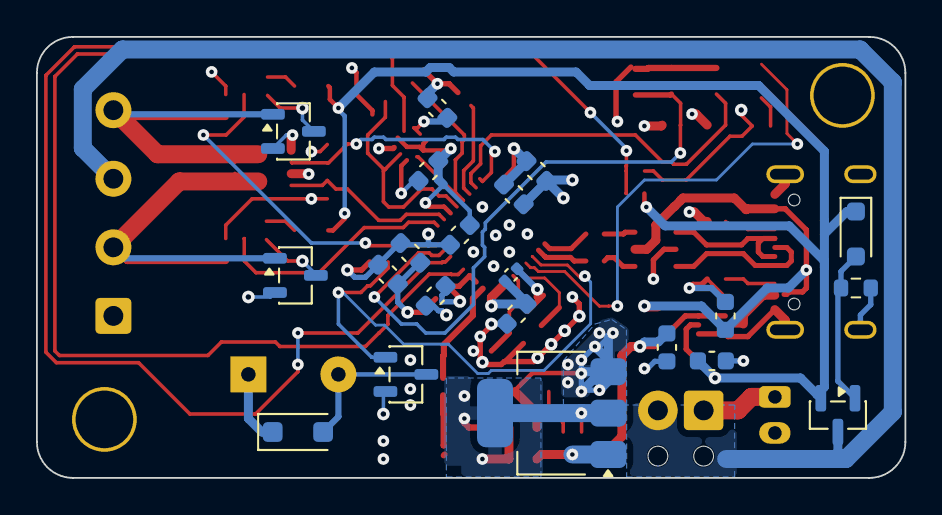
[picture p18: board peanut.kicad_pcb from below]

Board: 4 copper layers, 48.2 x 24.5 mm, 73 parts (21 on the bottom side), 44 nets.

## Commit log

2026-01-03 Initial commit.
    [peanut.kicad_pcb, peanut.kicad_sch, power.kicad_sch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]
2026-02-24 Assigned some actual parts and footprints to symbols.
    [peanut.kicad_sch, power.kicad_sch, pyro.kicad_sch]
2026-02-25 Footprint assignments for dual-channel NMOS; picked some more parts
    [TSM200N03DPQ33_RGG.stp, peanut.kicad_sch, power.kicad_sch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]
2026-02-25 More component MPNs
    [peanut.kicad_sch, power.kicad_sch, pyro.kicad_sch]
2026-04-27 feat: Finish schematic
    This commit "completes" the schematic to the best of my foresight for
    the moment. All components have BOM MPNs and footprints assigned. I have
    double checked pins on the 40MHz clock and that pin assignments on the
    MCU are valid. I have selected a chip antenna with high gain, added
    decoupling capacitors to the MCU, picked out terminal blocks and
    followed the Espressif schematic guide. A preliminary layout can be
    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
    [ACAG0201-2450-T.stp, CMI-0955-03TH.stp, peanut.kicad_sch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]
2026-04-28 feat: Initial layout
    I have roughed out the initial PCB layout. It is wider than I'd like,
    and not near a peanut shape. It appears the "start" and "panic" LEDs
    never had pins assigned to them. I think I will replace the MCU RX & TX
    with these instead, since I can still use the RX and TX as probe pads
    that way.
    [peanut.kicad_pcb, peanut.kicad_sch, power.kicad_sch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]
2026-04-28 bug: Fix missing connections to START/PANIC LEDs
    The START/PANIC LEDs now take over the UART interface. If UART is
    needed, using the pads of the LEDS should not be functionally different
    than using the test points.
    [peanut.kicad_pcb, peanut.kicad_sch]
2026-04-28 feat: Remove secondary crystal oscillator
    We will rely on the internal crystal oscillator: it is cheaper, saves me
    headaches routing the RF stuff and removes an unnecessary component.
    [peanut.kicad_pcb, peanut.kicad_sch]
2026-04-28 bug: Buzzer not connected
    Fixed the buzzer line not being connected to anything by replacing the
    PANIC LED with it. Buzzing during panic is equally acceptable, if not
    annoying, while debugging.
    [peanut.kicad_pcb, peanut.kicad_sch]
2026-04-29 feat: Mounting holes
    Added M3 mounting holes.
    [peanut.kicad_pcb, peanut.kicad_sch]
2026-04-29 feat: Better layout
    [peanut.kicad_pcb, peanut.kicad_sch, power.kicad_sch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]
2026-04-29 feat: Added necessary silkscreen information
    [peanut.kicad_pcb, peanut.kicad_sch]
2026-04-29 feat: Added inner layer pours
    [peanut.kicad_pcb, peanut.kicad_sch]
2026-04-29 feat: 100n capacitors to 0603
    Since there is sufficient space, the 100n capacitors have been increased
    to 0603 size and all placed on the back of the board. This allows the
    board to be squished in further slightly.
    [peanut.kicad_pcb, peanut.kicad_sch]
2026-04-29 feat: Shrink board
    Shrinks the board length-wise more.
    [peanut.kicad_pcb]
2026-04-29 feat: Verify component features
    Completed most of the review checklist for the initial revision. Routing
    can commence once design rules are updated.
    [peanut.kicad_pcb, peanut.kicad_sch, power.kicad_sch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]
2026-04-30 feat: Cheaper inductor
    Swapped inductor for one that is cheaper. Current board cost (minus JST
    connector since that is not available on Mouser) is $44.76 CAD in
    components.
    [SRN3015BTA-2R2M.stp, peanut.csv, peanut.kicad_pcb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]
2026-04-30 feat: Solder jumpers instead of capacitor footprint
    The boot and enable jumpers are now solder jumpers instead of capacitors
    footprints, which should make them easier to jump.
    [peanut.kicad_pcb, peanut.kicad_sch]
2026-04-30 feat: Add silkscreen logo
    Adds a board logo and my logo to the board silkscreen.
    [peanut.kicad_pcb]
2026-04-30 feat: Initial routing
    Initial, rough routing of traces.
    [peanut.kicad_pcb, peanut.kicad_sch]
2026-04-30 chore: Fix all DRC issues except RF routing
    [peanut.kicad_pcb]
2026-04-30 feat: Open Source Hardware silkscreen
    [peanut.kicad_pcb]
2026-05-01 chore: Mention min-diameter 29mm form-factor
2026-05-01 feat: Route the Bluetooth trace
    [peanut.kicad_pcb, peanut.kicad_sch]
2026-05-01 bug: Fix arming flaw
    Fixed the arming circuitry so that the ARM terminal prevents power going
    to the pyro channels. This means that the rest of the board can be
    powered on before arming, which is good because:
    - It allows configuring without arming
    - Software arming can still be done as a second stage
    - The MCU can be in low-power mode until told to arm over BLE
    [peanut.kicad_pcb, power.kicad_sch, pyro.kicad_sch]
2026-05-01 chore: Clean up routing
    Cleaned up some traces and added teardrops.
    [peanut.kicad_pcb, pyro.kicad_sch]
2026-05-01 chore: ignore gerbers
2026-05-01 chore: More MCU ground vias
    [peanut.kicad_pcb]
2026-05-01 chore: add dimensions
    [peanut.kicad_pcb]
2026-05-01 chore: fix inductor footprint size
    [peanut.kicad_pcb, peanut.kicad_sch]
2026-05-05 feat: Better arming circuit
    Improved the arming circuit connections so that both circuits are
    powered off until armed.
    [peanut.kicad_pcb, power.kicad_sch, pyro.kicad_sch]
2026-05-07 feat: Move USB closer to the edge.
    [peanut.kicad_pcb, peanut.kicad_sch]
2026-05-28 chore: add CHIP_EN capacitor
    [peanut.kicad_sch]
2026-05-28 chore: add flyback diode to buzzer
    [peanut.kicad_sch]
2026-05-28 chore: updated RF components to 0402
    [peanut.kicad_sch]
2026-05-28 chore: replace switching regulator with LDO
    [power.kicad_sch]
2026-05-28 chore: fix bulk capacitance value based on easymini selected value
    [power.kicad_sch]
2026-05-28 Fix ADC voltage monitoring to use 1:1 ratio
    [power.kicad_sch, pyro.kicad_sch]
2026-05-29 feat: improve reverse polarity protection circuit
    [power.kicad_sch]
2026-05-29 feat: change LDO again to something with better dropout voltage
    [power.kicad_sch]
2026-05-29 chore: re-annotate
    [peanut.kicad_sch, power.kicad_sch, pyro.kicad_sch]
2026-05-29 feat: changed pressure sensor to BMP581
    [BMP581.stp, peanut.kicad_sch, power.kicad_sch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]
2026-05-29 feat: new routing done
    [peanut.kicad_pcb, peanut.kicad_sch, power.kicad_sch]
2026-05-29 feat: Added copper keepout for antenna
    NOTE: did not follow the recommended layout exactly, so this is adapted
    as best as possible.
    [peanut.kicad_pcb]
2026-05-29 chore: resolve DRC errors
    [peanut.kicad_pcb, power.kicad_sch]
2026-05-29 chore: new BOM
    [peanut.csv]
2026-06-02 feat: add the maple leaf
    [peanut.kicad_pcb]
2026-06-02 feat: finished review; swapped battery lead polarity to match other rocket electronics
    [peanut.csv, peanut.kicad_pcb, peanut.kicad_sch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]
